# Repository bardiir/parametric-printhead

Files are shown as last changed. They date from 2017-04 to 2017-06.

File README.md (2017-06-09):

# parametric-printhead
Build of a parametric printhead encapsulation for the CTC Bizer Dual that replaces one extruder with a cooling assembly and makes it possible to fast-swap the printhead by using ethernet connectors.

## What this is about?
I've experienced a lot of cable breaks with the printhead of my CTC machine, most of them within the Thermocouple wires as they are not meant for a lot of movement. So I decided to replace the wires that run all the way down to the mainboard with a more flexible solution, ethernet cable. This offers me a possibility to easily exchange the printhead too as the connection is just clipped and the printhead only is fixed with two screws on the carriage. If the cable fails again it's not just a 10 seconds fix and a 1€ cost for the cable instead of having to open up the whole cable structure, dig out the failed cable and replace it complete with the thermocouple. They are not prohibitively expensive but they do cost more in the long run to replace.

## Mk1
I'm using Ethernet patch connector extension wires (http://amzn.to/2nQmoxb), cut them open and used the cables to connect the fan, extruder and heating element on the printhead with one set of these as well as every connection going to the mainboard with another set of these. In between the two ethernet sockets I'm then using 0,5m patch cables. I've matched everything in red and white to differentiate between the sockets but that is purely cosmetics.

## Mk2
This has been changed:
- Better air exhaust design, this was just a first proof of conecpt to see if everything works, the air outlet of Mk1 mainly cools the nozzle not the extruded filament, this is bad
- Custom PCB, using the patch extensions was just quick workaround
- Added some fuses - polyfuses for the heater wires going through ethernet so if one of the connections gets cut it doesn't result in an overload on the remaining one as well as an additional burn fuse on the PCB to prevent the heater current to leave safe levels alltogether

There also have been plans to do these:
- Have the Thermocouple read at the printhead not back at the mainboard, shield SPI bus from EMI noise  
-> Actually this did result in very bad behavior in all Tests, the error margin for the Thermocouple is low enough to work for this case anyway. However it is a little bit depending on the environment temperature this way which is actually good in this case as it errs to higher temperatures measured in hotter environments which lowers the print temperature and actually levels out the error caused by the environment in the first place. But this is only 1-2°C anyway.

- Have an expansion modifier for annnealing the part. Ideally this part, as it is in direct contact with hot elements of the printhead should be annealed to increase it's temperature stability, this however does cause some warping (see this video: https://www.youtube.com/watch?v=CZX8eHC7fws&t=141s), there should be a modifier to take care of this  
-> Currently using aluminium tape to shield the part, works like a charm, no annealing necessary

- Use nuts to screw fan duct and exhaust together  
-> It's now one part anyway, no need to screw it together, but maybe I'll create a Mk3 version that is screwed if someone can't or doesn't want to print big support structures.

## Future plans
- Make Exhaust clip-on and easily exchangeable to cater for various nozzle heights without changeing the whole printhead and to make it printable as an extra part, ideally without any supports

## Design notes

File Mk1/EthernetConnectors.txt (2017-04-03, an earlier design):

Connector 1 (White)
-------------------
Brown    | Heating Capsule +
Brown-W  | Heating Capsule -
Blue     | Stepper Motor Coil 1 +
Blue-W   | Stepper Motor Coil 1 -
Green    | Cooling Fan Extruder Heatsink +
Green-W  | Cooling Fan Extruder Heatsink -
Yellow   | Thermocouple +
Yellow-W | Thermocouple -
Shield   | GND

Connector 2 (Red)
-----------------
Brown    | Heating Capsule +
Brown-W  | Heating Capsule -
Blue     | Stepper Motor Coil 2 +
Blue-W   | Stepper Motor Coil 2 -
Green    | Cooling Fan Air Channel +
Green-W  | Cooling Fan Air Channel -
Yellow   | (Unused)
Yellow-W | (Unused)
Shield   | GND

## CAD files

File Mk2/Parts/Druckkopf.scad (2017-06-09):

/// --- RENDER SELECTION

//air_thingy();
air_thingy_support();
//top_plate();
render_printer_connectorplate = 0;

/// --- CALIBRATION VARIABLES

heatbrake_width = 45.8 + 0.5;
heatbrake_height = 12.9 + 0.2;
heatbrake_depth = 15.8 + 0.2;
heatbrake_sunk_at_mount = 3;

fan_width = 40 + 0.2;
fan_screw_distance = 32.3;
fan_screw_diameter = 2.9;
fan_distance_from_center = 7;
fan_screw_length = 5;
fan_lip_height = 5;

board_width = 45.1;
board_height = 33;
board_solder_offset = 2.5;
board_thickness = 1.7;
board_depth = 20-board_thickness;

printhead_height = 45.1;

clampscrew_distance_from_heatbrake_end = 44.8;
clampscrew_diameter = 3 + 0.5 ;
clampscrew_distance_between = 10.5;

air_channel_width = 7;
air_channel_from_heatbrake_end = 16.4;

front_space = 20;

wall_thickness = 1.6;

nozzle_below_heatbrake = 25;
nozzle_distance_from_heatbrake_end = 61.5;
nozzle_diameter = 7;
nozzle_distance_from_heatbrake_back = 9.5;

exhaust_bed_clearance = 2;
exhaust_nozzle_clearance = 20;
exhaust_width = 5;

filament_diameter = 3.5 + 0.2;
filament_tube_diameter = 9 + 0.2;
filament_tube_guide_height = 6.5;

stepper_motor_depth = 34;
stepper_motor_width = 42.5;
stepper_motor_connector_depth = 10.3 + 0.5;
stepper_motor_connector_width = 16.3 + 0.5;

top_plate_height = 5;

/// --- CALCULATED

fan_screw_distance_from_wall = (fan_width - fan_screw_distance)/2;
fan_screw_block_size = fan_screw_diameter+fan_screw_distance_from_wall;

module top_plate() {
    difference() {
        union() {
            translate([heatbrake_width-fan_distance_from_center+wall_thickness,-wall_thickness,printhead_height])
            cube([stepper_motor_width+fan_distance_from_center-wall_thickness,heatbrake_depth+(fan_width-front_space-heatbrake_depth)+wall_thickness*3,top_plate_height]);
            
            translate([heatbrake_width-(board_width+wall_thickness*2),heatbrake_depth+(fan_width-front_space-heatbrake_depth)+wall_thickness*2,printhead_height])
            cube([stepper_motor_width+heatbrake_width+wall_thickness,stepper_motor_depth-(fan_width-heatbrake_depth-front_space+wall_thickness*2)-(board_thickness+wall_thickness*2+5),top_plate_height]);
            
            translate([heatbrake_width,heatbrake_depth,printhead_height])
            cube([stepper_motor_width,stepper_motor_depth,top_plate_height]);
            
            translate([nozzle_distance_from_heatbrake_end,heatbrake_depth-nozzle_distance_from_heatbrake_back,printhead_height+top_plate_height])
            cylinder(d=filament_tube_diameter+wall_thickness*2,h=filament_tube_guide_height,$fn=100);
        }
        
        //filament cutout
        translate([nozzle_distance_from_heatbrake_end,heatbrake_depth-nozzle_distance_from_heatbrake_back,printhead_height])
        cylinder(d=filament_diameter,h=filament_tube_guide_height+top_plate_height,$fn=100);
        
        //tube connector cutout
        translate([nozzle_distance_from_heatbrake_end,heatbrake_depth-nozzle_distance_from_heatbrake_back,printhead_height+top_plate_height])
        cylinder(d=filament_tube_diameter,h=filament_tube_guide_height,$fn=100);
        
        //board cutout
        translate([heatbrake_width-(board_width+wall_thickness)+1,heatbrake_depth+stepper_motor_depth-board_depth-wall_thickness-board_solder_offset,printhead_height-board_height/2])
        cube([board_width-2,board_depth-board_thickness,board_height]);
        
        //stepper connector cutout
        translate([heatbrake_width+((stepper_motor_width-stepper_motor_connector_width)/2),heatbrake_depth+stepper_motor_depth-stepper_motor_connector_depth,stepper_motor_width])
        cube([stepper_motor_connector_width,stepper_motor_connector_depth,10]);
        
        //clamp screw holes
        translate([clampscrew_distance_from_heatbrake_end,(heatbrake_depth-clampscrew_distance_between)/2,heatbrake_height])
        cylinder(d=clampscrew_diameter,h=printhead_height,$fn=100);
        translate([clampscrew_distance_from_heatbrake_end,(heatbrake_depth-clampscrew_distance_between)/2+clampscrew_distance_between,heatbrake_height])
        cylinder(d=clampscrew_diameter,h=printhead_height,$fn=100);
    }
}

module air_thingy_support()
{
    union() {
    translate([0,-air_channel_width,-nozzle_below_heatbrake+exhaust_bed_clearance])
    cube([air_channel_from_heatbrake_end-0.4, air_channel_width*2+heatbrake_depth+0.6, heatbrake_height - 0.4 +nozzle_below_heatbrake-exhaust_bed_clearance]);
    
    #translate([0,heatbrake_depth+air_channel_width+0.6,-nozzle_below_heatbrake+exhaust_bed_clearance])
    cube([heatbrake_width, stepper_motor_depth-air_channel_width, heatbrake_height - 0.4 +nozzle_below_heatbrake-exhaust_bed_clearance]);
    }
}
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

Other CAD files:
Mk1/Druckkopf.scad
Mk1/Guide.scad

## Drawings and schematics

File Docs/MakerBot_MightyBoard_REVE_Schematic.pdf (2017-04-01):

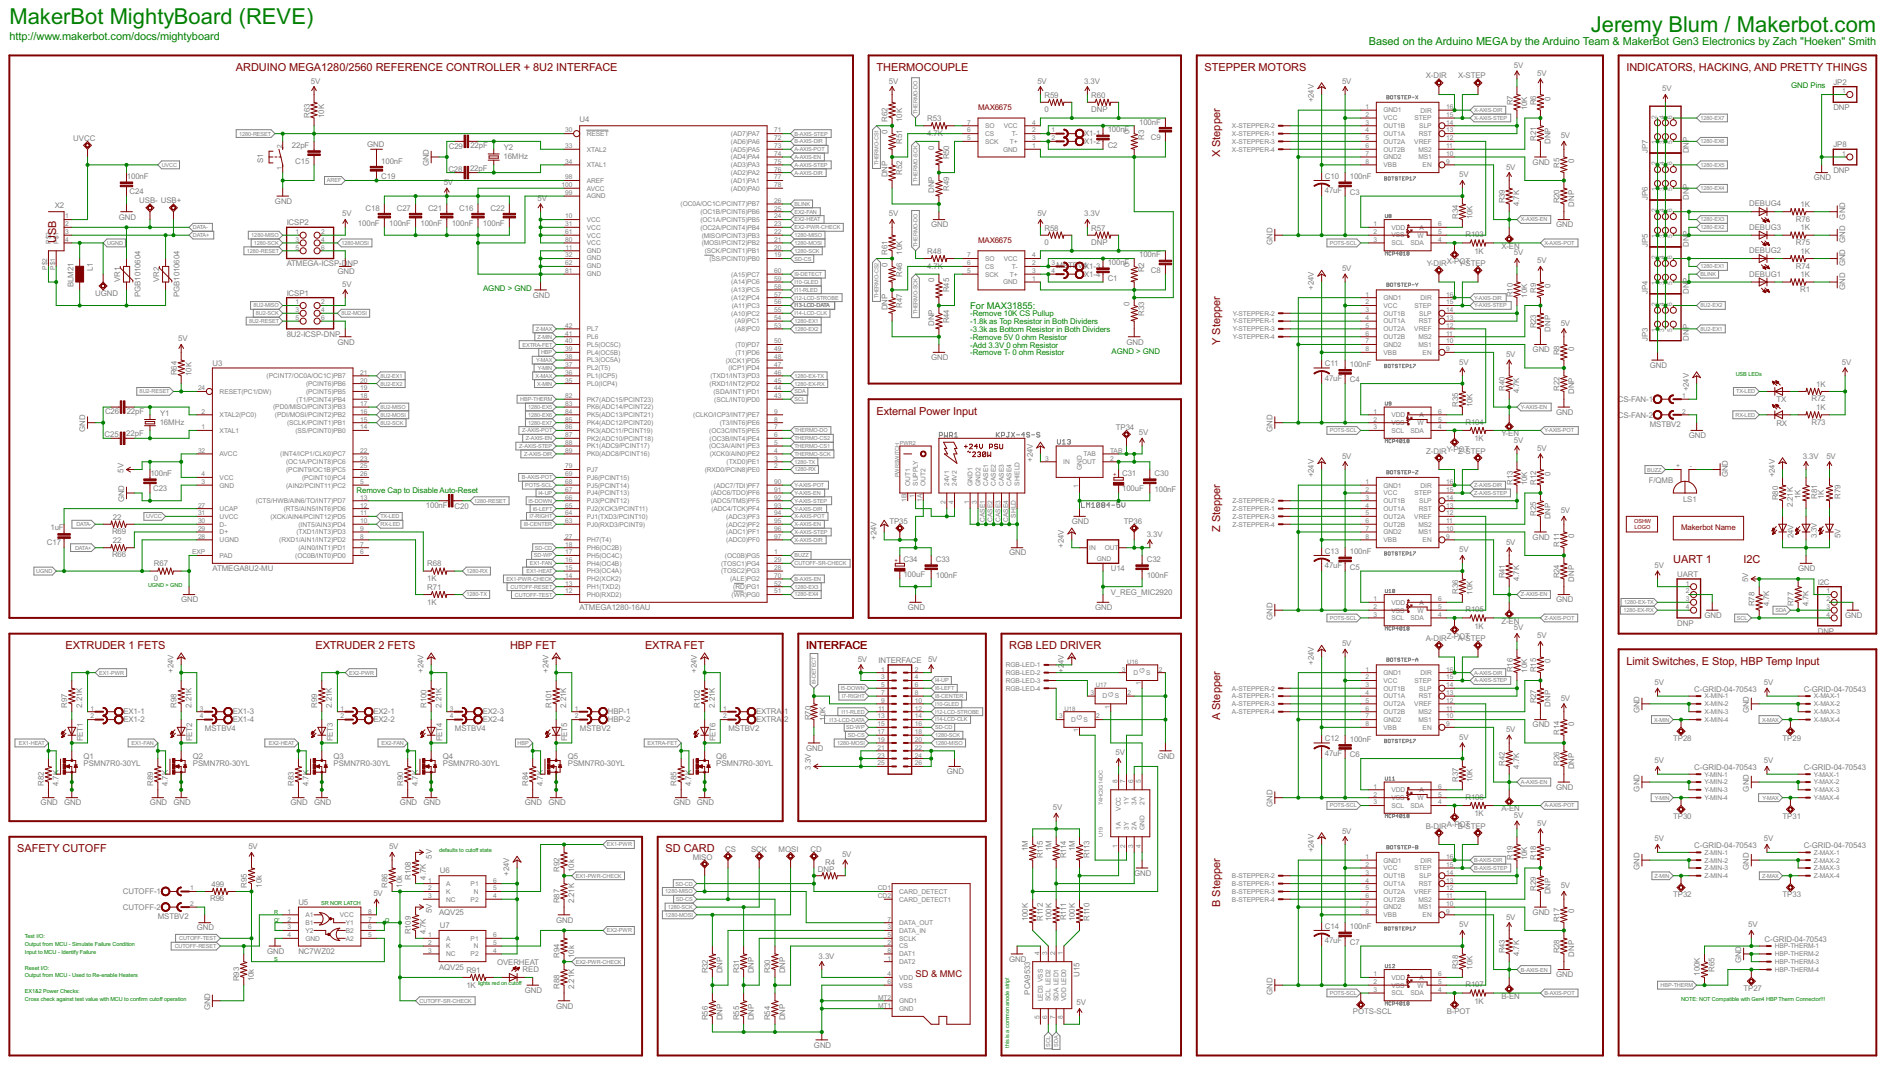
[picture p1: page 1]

USB MakerBot MightyBoard (REVE)

ARDUINO MEGA1280/2560 REFERENCE CONTROLLER + 8U2 INTERFACE

THERMO-DO

THERMO-SCK

AGND > GND For MAX31855: -Remove 10K CS Pullup

Y Stepper Z Stepper A Stepper B Stepper

-1.8k as Top Resistor in Both Dividers
-3.3k as Bottom Resistor in Both Dividers
-Remove 5V 0 ohm Resistor
-Add 3.3V 0 ohm Resistor
-Remove T- 0 ohm Resistor

RGB-LED-1 RGB-LED-2 RGB-LED-3 RGB-LED-4

Limit Switches, E Stop, HBP Temp Input

defaults to cutoff state

HBP-THERM-1 HBP-THERM-2 HBP-THERM-3 HBP-THERM-4 CS

Test I/O: Output from MCU - Simulate Failure Condition

Input to MCU - Identify Failure Reset I/O: Output from MCU - Used to Re-enable Heaters EX1&2 Power Checks: Cross check against test value with MCU to confirm cutoff operation

3.3V DNP DNP DNP DNP

this is a common anode strip!

lights red on cutoff

NOTE: NOT Compatible with Gen4 HBP Therm Connector!!!

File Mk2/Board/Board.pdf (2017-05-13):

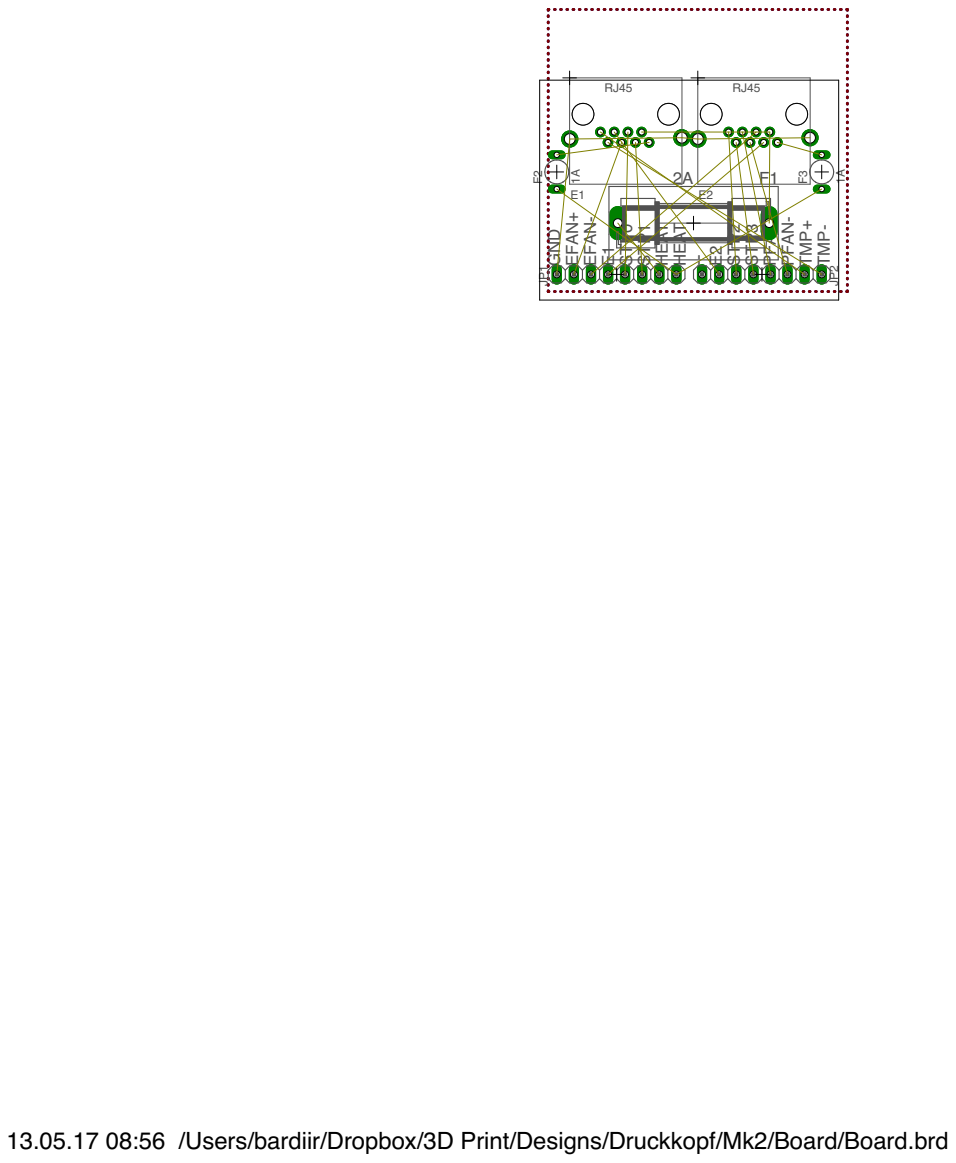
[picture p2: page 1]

EFAN+ EFAN- E1STP0 STP1 HEAT HEAT

--E2STP2 STP3 PFAN+ PFAN- TMP+ TMP-

13.05.17 08:56 /Users/bardiir/Dropbox/3D Print/Designs/Druckkopf/Mk2/Board/Board.brd

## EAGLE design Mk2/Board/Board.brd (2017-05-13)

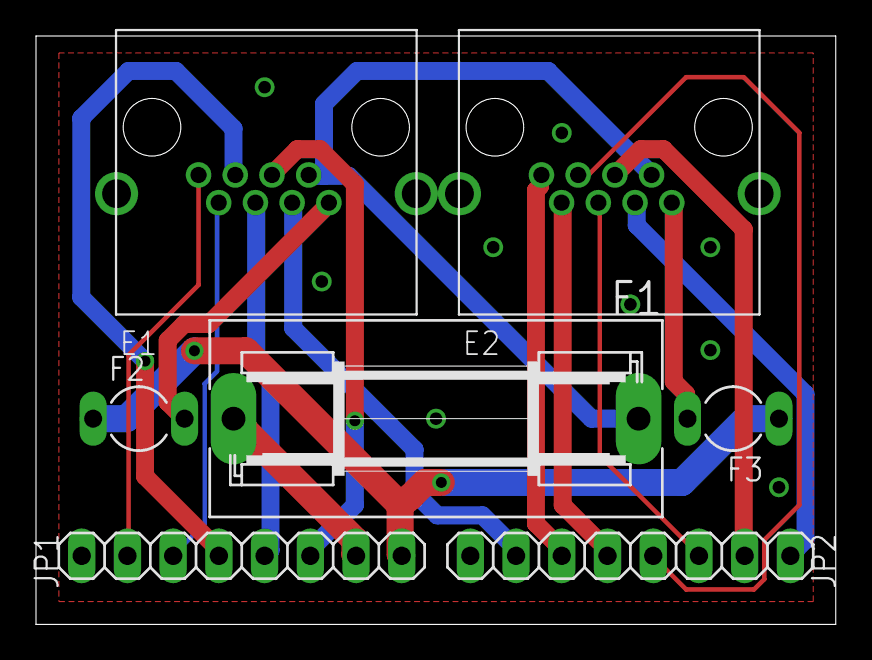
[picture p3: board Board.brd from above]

Board: 2 copper layers, 44.4 x 32.7 mm, 7 parts (0 on the bottom side), 18 nets.

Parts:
E1, E2: RJ45
F1: 2A; SH22,5A
F2, F3: 1A; POLYFUSE
JP1, JP2: 1X08

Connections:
GND: E1.S@1, E1.S@2, E2.S@1, E2.S@2, JP1.8, JP2.8
unnamed: E1.8, F2.2
unnamed: E2.8, F3.2
unnamed: E1.7, E2.7, F1.1
unnamed: F2.1, F3.1, JP1.1
unnamed: F1.2, JP1.2
unnamed: E1.1, JP1.7
unnamed: E1.2, JP1.6
unnamed: E1.3, JP1.5
unnamed: E1.4, JP1.4
unnamed: E1.5, JP1.3
unnamed: E1.6, JP2.7
unnamed: E2.1, JP2.6
unnamed: E2.2, JP2.5
unnamed: E2.3, JP2.4
unnamed: E2.4, JP2.3
unnamed: E2.5, JP2.2
unnamed: E2.6, JP2.1

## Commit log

2017-03-31 ignore 3d printing generated files
2017-04-01 added cable box
    [Druckkopf.scad]
2017-04-01 connect supports to save printtime by generating less perimeters
    [Druckkopf.scad]
2017-04-01 add ethernet connectors connection definition
2017-04-01 mightyboard schematic
2017-04-01 testprint, adjusted measurements with tolerances and thicker walls for more stability
    [Druckkopf.scad]
2017-04-01 test print, adjusted values
    [Druckkopf.scad]
2017-04-01 made it possible to print singular parts, testprints, finetuning values
    [Druckkopf.scad]
2017-04-01 easier render selection for different parts
    [Druckkopf.scad]
2017-04-02 opened up ethernet sockets to insert ethernet port with cables attached and created printer side plate
    [Druckkopf.scad]
2017-04-02 add filament guide to printer plate
    [Druckkopf.scad]
2017-04-03 finalized printhead 1, testprints for #2 started, adjusted values and added a calibration notes file to keep different measurements for the printheads
    [Druckkopf.scad]
2017-04-03 having the MAX6675 at the print head is not a viable option, the SPI bus is easily interrupted by the extruders stepper motor control nearby, creating noise in the temperature reads and sometimes eve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
2017-04-03 restructured folders
    [Druckkopf.scad]
2017-04-03 too late…
    [Druckkopf.scad]
2017-04-06 cleanup exhaust, generate cutout to prevent sagging exhaust and make fitting over an installed nozzle easier
    [Druckkopf.scad]
2017-04-06 improve airflow by increasing lower cutout diameter on the exhaust
    [Druckkopf.scad]
2017-04-07 measurements for second printhead
2017-05-13 changed parameters after testprints
    [Druckkopf.scad]
2017-05-13 filament guide plate for the bowden tube to the printhead
    [Guide.scad]
2017-05-13 ethernet board for Mk2 Printhead
    [Board.brd, Board.sch]
2017-05-13 moved the appropiate files to the Mk1 Printhead design, Mk2 will use a different cable layout and different parameters for the design
2017-05-13 board design
    [Board.brd, Board.sch]
2017-06-07 board finalization
2017-06-07 printhead Mk2 initial version
    [Druckkopf.scad]
2017-06-08 boards a a bit wider, also they do have solder joints that are not flush *facepalm*
    [Druckkopf.scad]
2017-06-08 opening not always towards nozzle, enlongening cutout cube to make wall break every time
    [Druckkopf.scad]
2017-06-08 clearance issue with aluminium printhead sled
    [Druckkopf.scad]
2017-06-08 enlarge cutout in cable chamber lid for top plate to make space for the moved board
    [Druckkopf.scad]
2017-06-09 wall thickness changed to 1.6 to better match the 0.4 nozzle currently installed, also added some manually created support as a modifier
    [Druckkopf.scad]
2017-06-09 give support block a bit more space so it doesnt adhere to the exhaust when printing
    [Druckkopf.scad]
